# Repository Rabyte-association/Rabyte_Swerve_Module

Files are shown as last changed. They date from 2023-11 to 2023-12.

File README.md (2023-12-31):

# Rabyte_Swerve_Module

---

#8127's custom swerve module design and documentation

## Basic characteristics

- as metric as possibile
- using NEOs for both driving and steering
- using Redux HELIUM Canandcoders
- custom polyurethane cast wheels with printed cores
- 30x60mm profiles for frame
- some 3D printed parts
- gears are modified off-the-shelf metric gears
- 7:64 steering ratio
- 1:7 or 4:21 drive ratio (1 gear swap)
- the design is based on the SDS mk4.

## **[Onshape link](https://cad.onshape.com/documents/77f17ba6a9909df0f0190ebf/w/6d8127f64ed0d1f2707c88a1/e/b61e76f2111f9b8cf438d247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)**

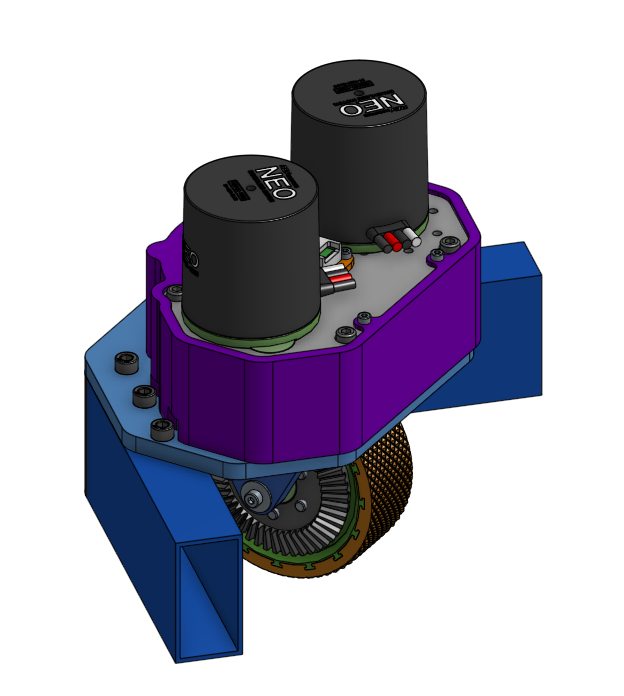
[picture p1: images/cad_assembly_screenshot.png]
cad


## December updates

- 3d printed cover
- new wheel and mould design
- ctre cancoder configuraton
- botom bracket instead of nuts
- config without frame profiles, for easier cad asembly
- added neo spacers, for more clearance

## Drivebase

We designed custom drivebase based on our modules, we are planing to use it in competition.
Onshape link: [drivebase cad link](https://cad.onshape.com/documents/012b6aa6ca8f98a975c3e93b/w/842512061215ac90e2240268/e/b5b0c5cf1ca33fb7e982671a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)
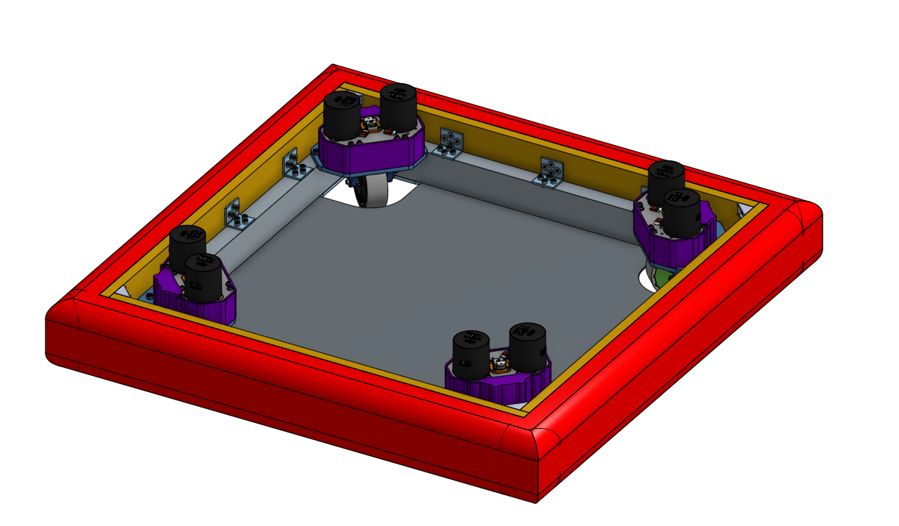
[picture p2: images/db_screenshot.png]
bd


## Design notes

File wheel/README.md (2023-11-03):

# Custom wheels

---

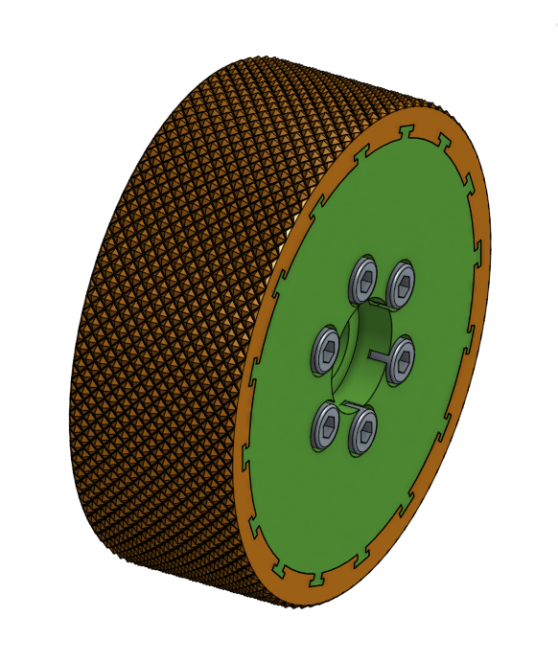
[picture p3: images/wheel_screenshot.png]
wheel


We designed custom 3D printed wheeel with tires casted out of polyurethane. We also did some experiments on how to cast such wheels.

Both  hub and mould are 3D printed. We used 70 shore A polyurethane. That is probably too hard. For the mould release we recomend polivynyl alcohol(pva).

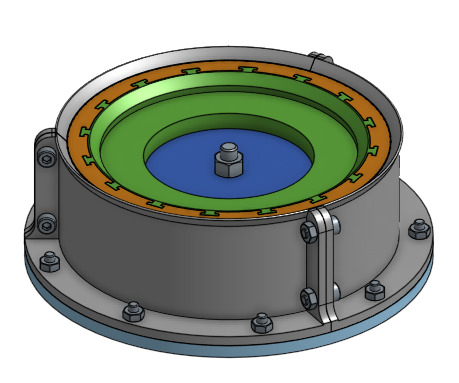
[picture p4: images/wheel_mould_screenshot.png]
mould


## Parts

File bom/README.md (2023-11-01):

# Bill of materials

List of all the necessary parts for one module.

**[google sheets](https://docs.google.com/spreadsheets/d/1GIMMn_G_28G_MlKw39UDYXvYzshxwfw3fDms4F0evjY/edit?usp=sharing)**

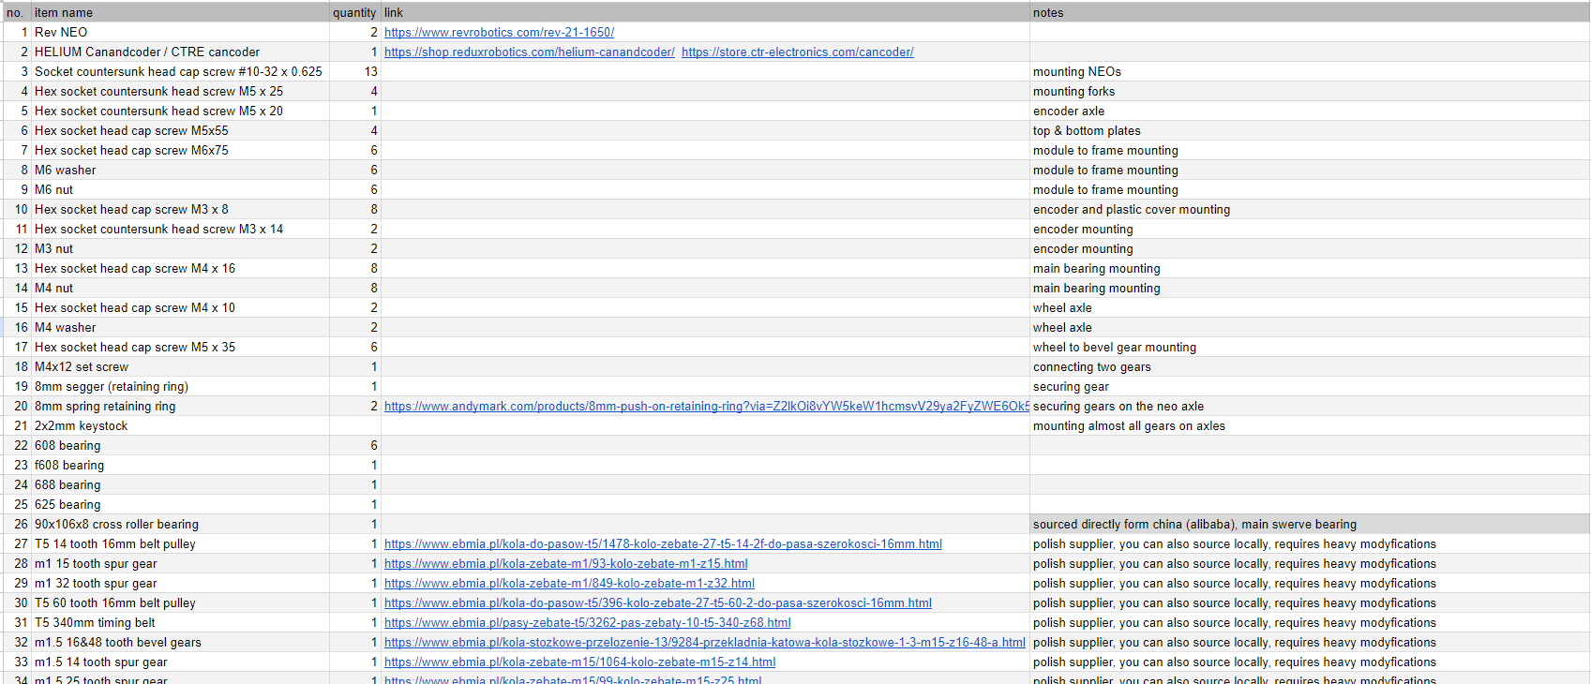
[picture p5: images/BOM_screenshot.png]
sheets


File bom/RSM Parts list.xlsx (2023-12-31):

no. | item name | quantity | link | notes
1 | Rev NEO | 2 | https://www.revrobotics.com/rev-21-1650/
2 | HELIUM Canandcoder / CTRE cancoder | 1 | https://shop.reduxrobotics.com/helium-canandcoder/ https://store.ctr-electronics.com/cancoder/
3 | Socket countersunk head cap screw #10-32 x 0.625 | 13 |  | mounting NEOs
4 | Hex socket countersunk head screw M5 x 25 | 4 |  | mounting forks
5 | Hex socket countersunk head screw M5 x 20 | 1 |  | encoder axle
6 | Hex socket head cap screw M5x55 | 4 |  | top & bottom plates
7 | Hex socket head cap screw M6x75 | 6 |  | module to frame mounting
8 | M6 washer | 6 |  | module to frame mounting
9 | M6 nut | 6 |  | module to frame mounting
10 | Hex socket head cap screw M3 x 8 | 8 |  | encoder and plastic cover mounting
11 | Hex socket countersunk head screw M3 x 14 | 2 |  | encoder mounting
12 | M3 nut | 2 |  | encoder mounting
13 | Hex socket head cap screw M4 x 16 | 8 |  | main bearing mounting
14 | M4 nut | 8 |  | main bearing mounting
15 | Hex socket head cap screw M4 x 10 | 2 |  | wheel axle
16 | M4 washer | 2 |  | wheel axle
17 | Hex socket head cap screw M5 x 35 | 6 |  | wheel to bevel gear mounting
18 | M4x12 set screw | 1 |  | connecting two gears
19 | 8mm segger (retaining ring) | 1 |  | securing gear
20 | 8mm spring retaining ring | 2 | https://www.andymark.com/products/8mm-push-on-retaining-ring | securing gears on the neo axle
21 | 2x2mm keystock |  |  | mounting almost all gears on axles
22 | 608 bearing | 6
23 | f608 bearing | 1
24 | 688 bearing | 1
25 | 625 bearing | 1
26 | 90x106x8 cross roller bearing | 1 |  | sourced directly form china (alibaba), main swerve bearing
27 | T5 14 tooth 16mm belt pulley | 1 | https://www.ebmia.pl/kola-do-pasow-t5/1478-kolo-zebate-27-t5-14-2f-do-pasa-szerokosci-16mm.html | polish supplier, you can also source locally, requires heavy modyfications
28 | m1 15 tooth spur gear | 1 | https://www.ebmia.pl/kola-zebate-m1/93-kolo-zebate-m1-z15.html | polish supplier, you can also source locally, requires heavy modyfications
29 | m1 32 tooth spur gear | 1 | https://www.ebmia.pl/kola-zebate-m1/849-kolo-zebate-m1-z32.html | polish supplier, you can also source locally, requires heavy modyfications
30 | T5 60 tooth 16mm belt pulley | 1 | https://www.ebmia.pl/kola-do-pasow-t5/396-kolo-zebate-27-t5-60-2-do-pasa-szerokosci-16mm.html | polish supplier, you can also source locally, requires heavy modyfications
31 | T5 340mm timing belt | 1 | https://www.ebmia.pl/pasy-zebate-t5/3262-pas-zebaty-10-t5-340-z68.html | polish supplier, you can also source locally, requires heavy modyfications
32 | m1.5 16&48 tooth bevel gears | 1 | https://www.ebmia.pl/kola-stozkowe-przelozenie-13/9284-przekladnia-katowa-kola-stozkowe-1-3-m15-z16-48-a.html | polish supplier, you can also source locally, requires heavy modyfications
33 | m1.5 14 tooth spur gear | 1 | https://www.ebmia.pl/kola-zebate-m15/1064-kolo-zebate-m15-z14.html | polish supplier, you can also source locally, requires heavy modyfications
34 | m1.5 25 tooth spur gear | 1 | https://www.ebmia.pl/kola-zebate-m15/99-kolo-zebate-m15-z25.html | polish supplier, you can also source locally, requires heavy modyfications
35 | m1.5 50 tooth spur gear | 1 | https://www.ebmia.pl/kola-zebate-m15/1785-kolo-zebate-m15-z50.html | polish supplier, you can also source locally, requires heavy modyfications
36 | m1.5 16 tooth spur gear | 1 | https://www.ebmia.pl/kola-zebate-m15/2136-kolo-zebate-m15-z16.html | polish supplier, you can also source locally, requires heavy modyfications, for highr gear ratio
37 | m1.5 12 tooth spur gear | 1 | https://www.ebmia.pl/kola-zebate-m15/211247-kolo-zebate-m15-z12.html | polish supplier, you can also source locally, requires heavy modyfications, for lower gear ratio
38 | top plate | 1 |  | fully custom, aluminium
39 | bottom plate | 1 |  | fully custom, aluminium
40 | power fork | 1 |  | fully custom, steel
41 | passive fork | 1 |  | fully custom, steel
42 | steering axle | 1 |  | fully custom, steel
43 | encoder axle | 1 |  | fully custom, steel
44 | bevel gear axle | 1 |  | fully custom, steel
45 | wheel axle | 1 |  | fully custom, steel
46 | top main bearing mount | 1 |  | fully custom, steel
47 | bottom main bearing mount | 1 |  | fully custom, steel
48 | standoff | 4 |  | fully custom, steel
49 | frame profiles | 2 |  | depends on the design of your robot, we recommend steel 30x60mm
50 | wheel with cast tire | 1 |  | fully custom, 3D printed & cast
51 | encoder mount | 1 |  | fully custom, 3D printed
52 | end cap | 1 |  | fully custom, 3D printed, optional
53 | wheel spacer 1 | 1 |  | fully custom, 3D printed
54 | wheel spacer 2 | 1 |  | fully custom, 3D printed
55
56
57
58
59
60
61
62
63
64
65
66
67
68
69
70
71
72
73
74
75
76
77
78
79
80
81
82
83
84
85
86
87
88
89
90
91
92
93
94
95
96
97
98
99
100
101
102
103
104
105
106
107
108
109
110
111
112
113
114
115
116
117
118
119
120
121
122
123
124
125
126
127
128
129
130
131
132
133
134
135
136
137
138
139
140
141
142
143
144
145
146
147
148
149
150
151
152
153
154
155
156
157
158
159
160
161
162
163
164
165
166
167
168
169
170
171
172
173
174
175
176
177
178
179
180
181
182
183
184
185
186
187
188
189
190
191
192
193
194
195
196
197
198
199
200
201
202
203
204
205
206
207
208
209
210
211
212
213
214
215
216
217
218
219
220
221
222
223
224
225
226
227
228
229
230
231
232
233
234
235
236
237
238
239
240
241
242
243
244
245
246
247
248
249
250
251
252
253
254

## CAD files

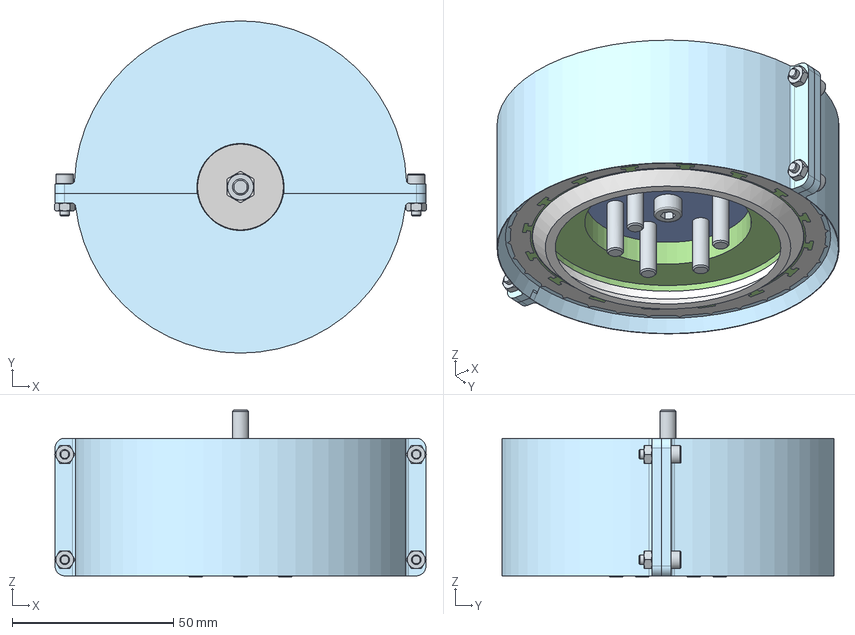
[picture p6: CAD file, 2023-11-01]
wheel/Rabyte_Swerve_Module-wheel_mould_assembly.step
115.4 x 103.0 x 51.7 mm
Hex nut grade A & B M5x0.8
Hex socket head cap screw M3x0.50 x 10 x 4
Hex socket head cap screw M5x0.80 x 35 x 6
Hex nut grade A & B M3x0.5 x 4
tire
hub

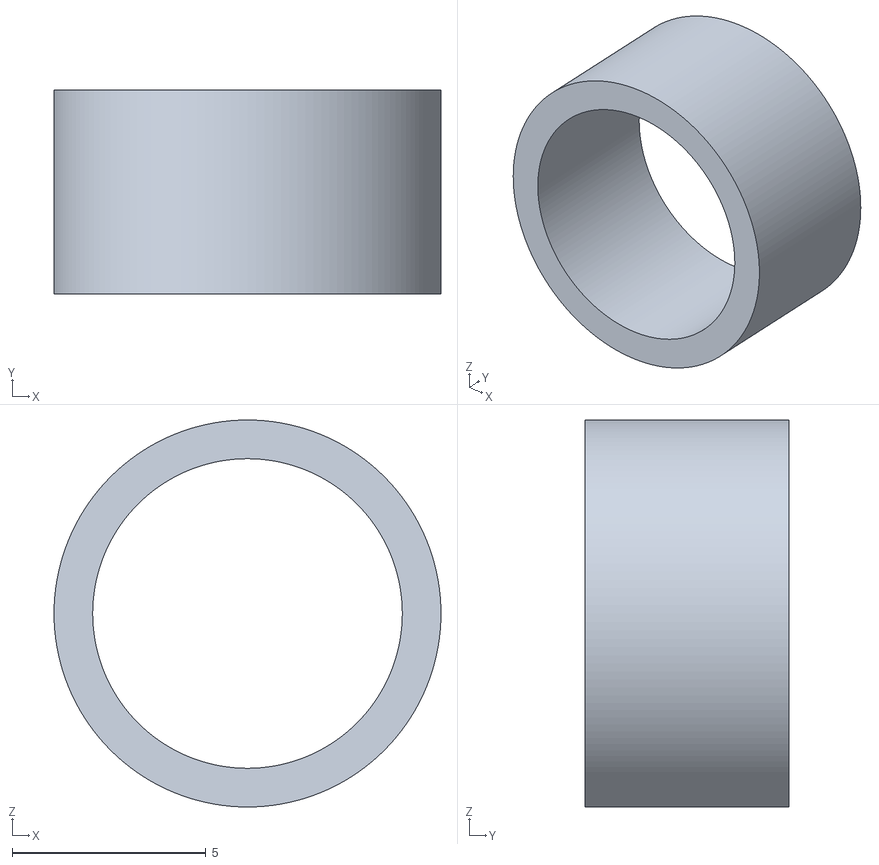
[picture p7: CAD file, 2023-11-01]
3d_print/RSM - main axle - spacer.stl
10.0 x 5.27 x 10.0

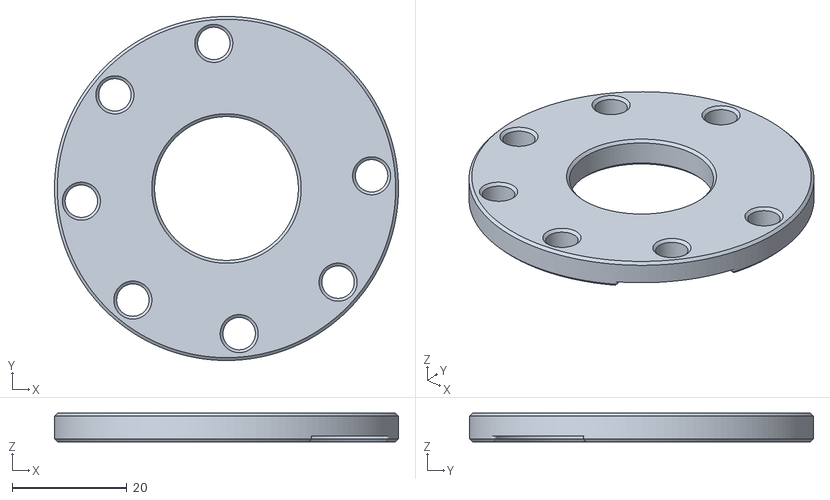
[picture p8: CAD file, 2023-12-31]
3d_print/RSM - neo spacer steer.stl
60.0 x 60.0 x 5.00

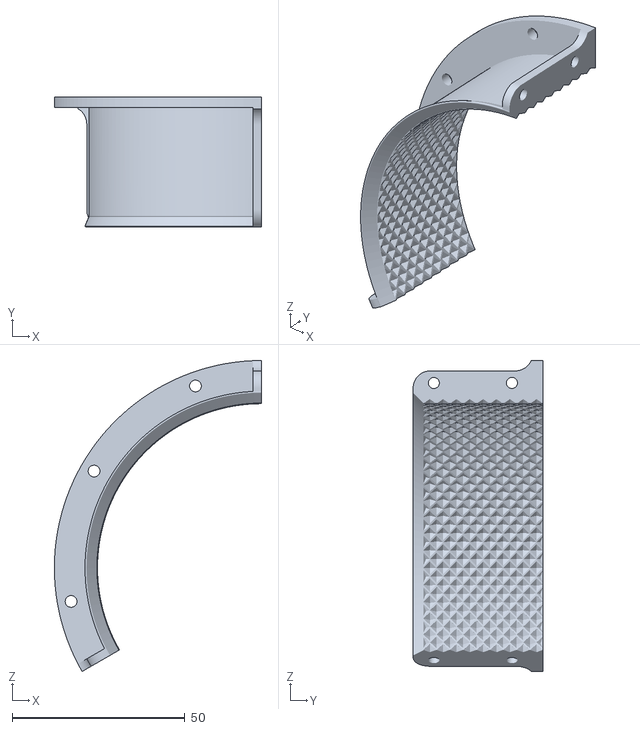
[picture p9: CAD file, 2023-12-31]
wheel/mould - Part 4.stl
60.0 x 37.7 x 90.0

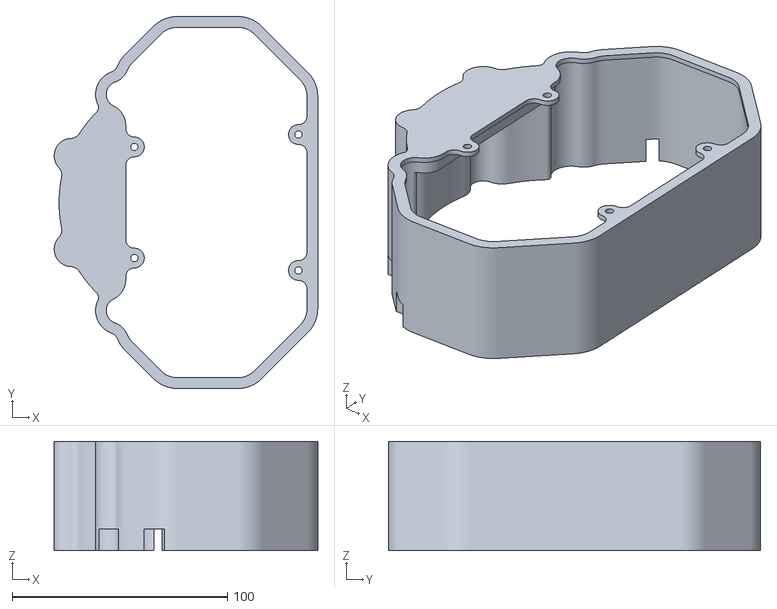
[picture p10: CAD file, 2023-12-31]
3d_print/RSM - cover.stl
122.4 x 172.8 x 50.8

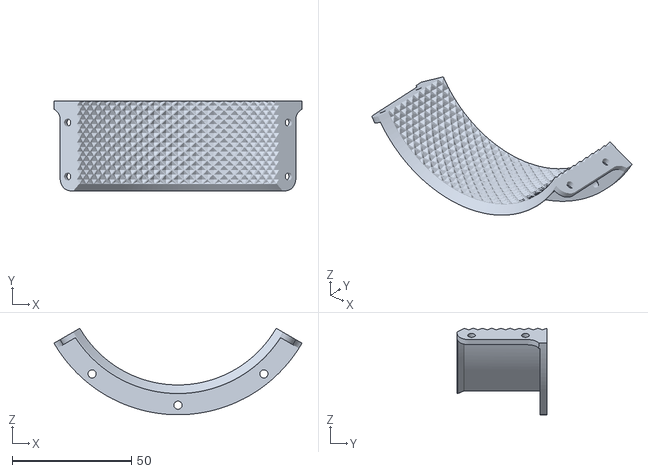
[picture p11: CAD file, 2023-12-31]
wheel/mould - Part 3.stl
103.9 x 37.7 x 36.2

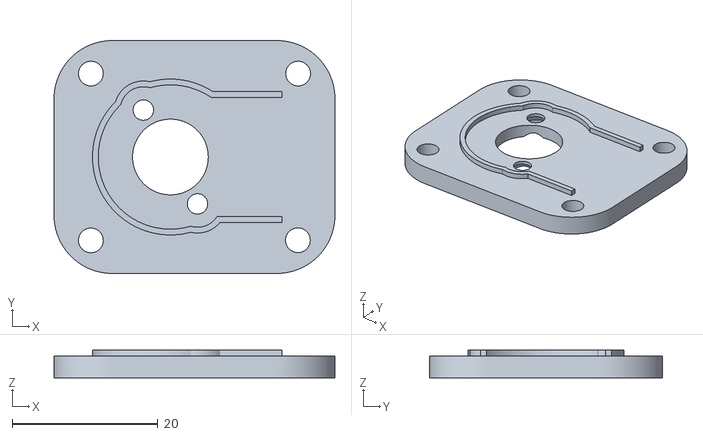
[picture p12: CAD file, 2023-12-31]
3d_print/RSM - canandcoder mount.stl
38.6 x 32.0 x 3.80

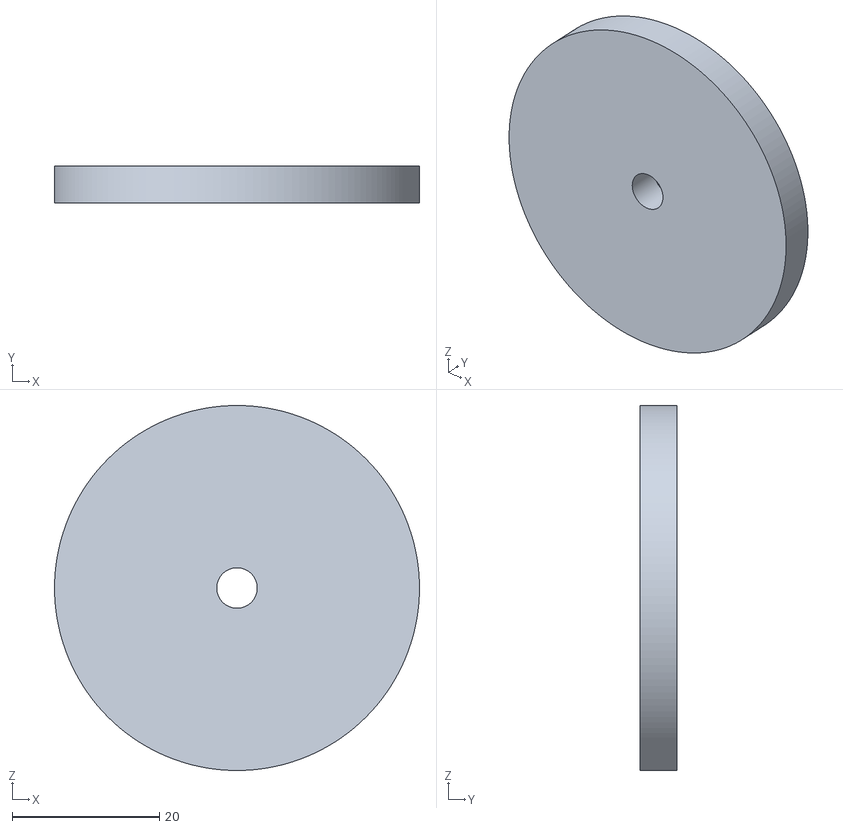
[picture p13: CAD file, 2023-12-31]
wheel/mould - Part 5.stl
49.6 x 5.00 x 49.6

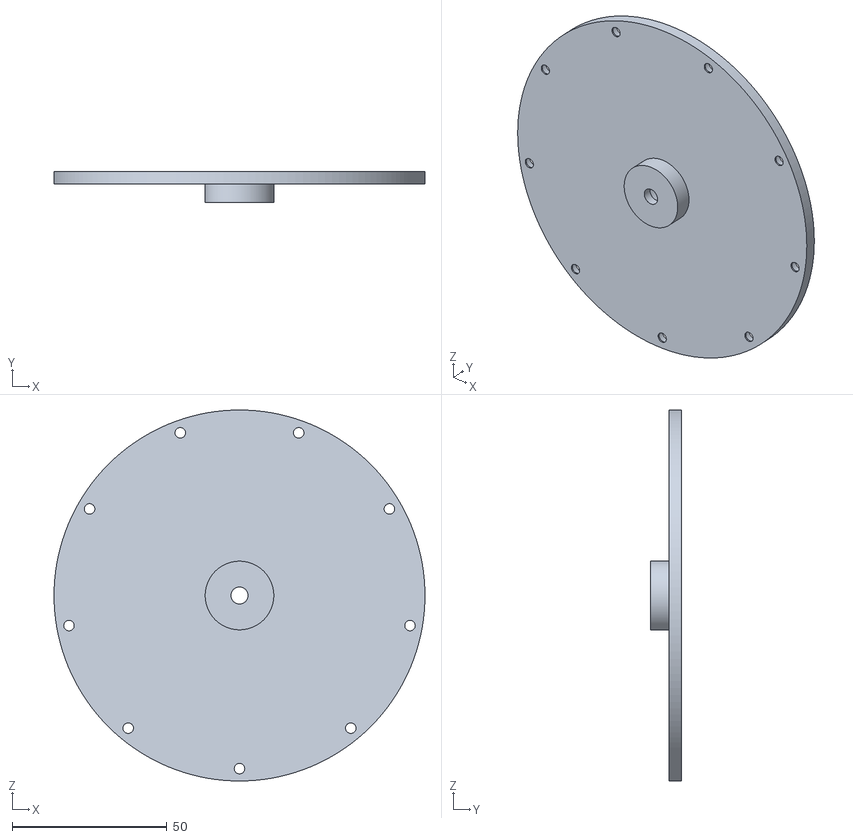
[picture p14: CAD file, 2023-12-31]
wheel/mould - Part 1.stl
120.0 x 10.0 x 120.0

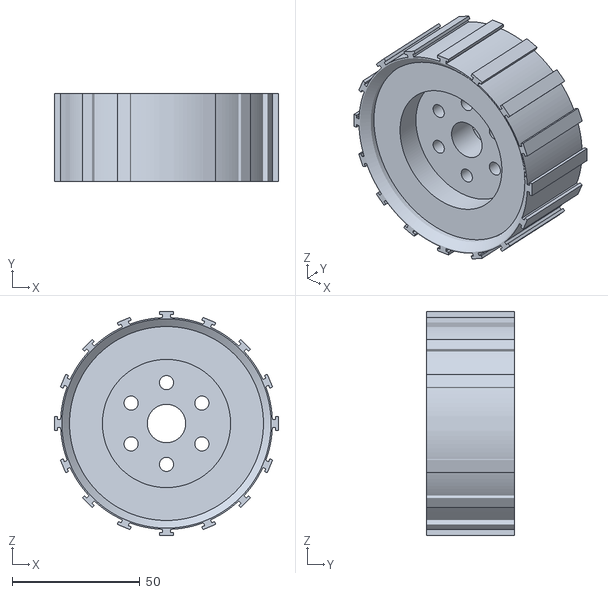
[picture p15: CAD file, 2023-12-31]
wheel/RSM-wheel_hub.stl
87.7 x 34.7 x 87.7

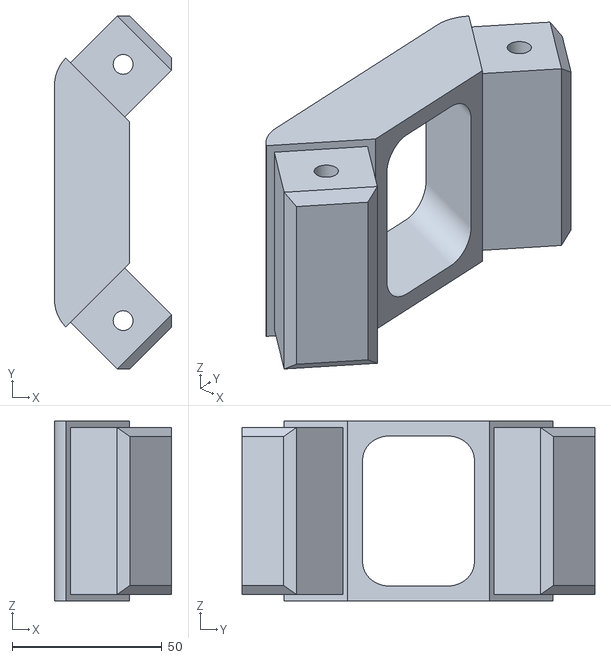
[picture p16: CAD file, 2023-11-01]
3d_print/RSM - end cap.stl
39.0 x 117.7 x 60.0

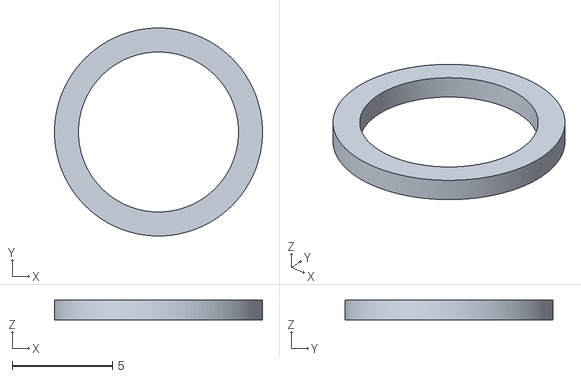
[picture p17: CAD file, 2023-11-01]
3d_print/RSM - 608 spacer - 1mm spacer.stl
10.4 x 10.4 x 1

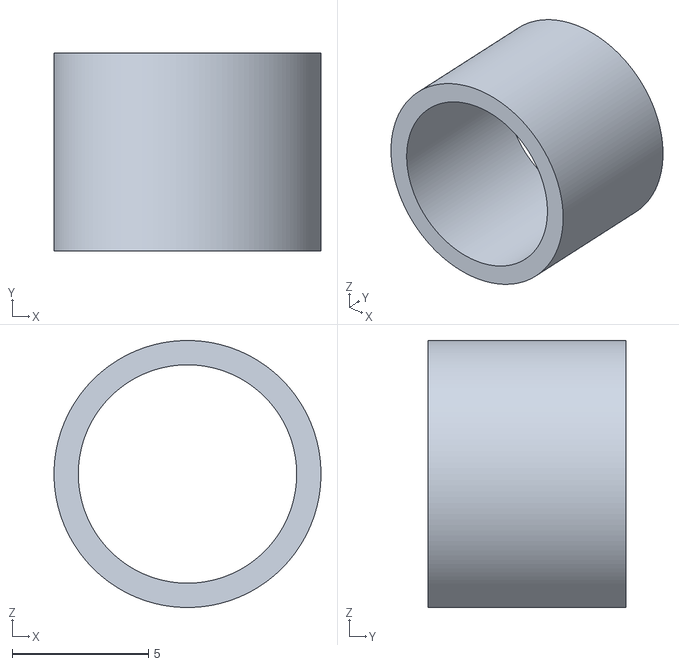
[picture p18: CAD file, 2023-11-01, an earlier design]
3d_print/RSM - main axle - spacer (1).stl
9.78 x 7.27 x 9.78

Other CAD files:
3d_print/RSM - cancoder mount.stl
wheel/mould - Part 2.stl
3d_print/RSM - neo spacer drive.stl

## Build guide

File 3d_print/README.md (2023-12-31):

# 3D printed parts

---
Some of the parts in the module are 3D printed.
Printing settings:

- PLA is **not** good enough
- around 5 walls, for strength
- infill around 50%, also for strength
- supports: not required for most parts

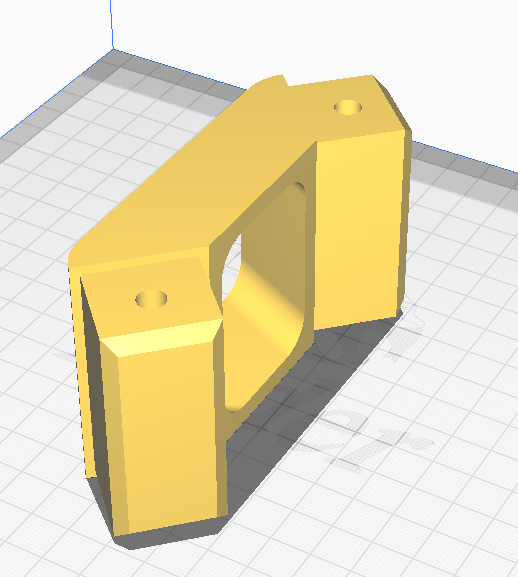
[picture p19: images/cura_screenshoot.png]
cura


As a side note, we printed the whole set of gears, forks and plates and it mostly works. Of course we don't recomend using it in the competiton, however it was a great resource for the programming team while we were waiting for the machined parts.

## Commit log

2023-11-01 cad upload
    [RSM-1mm_608_spacer.stl, RSM-beam_end_cap.stl, RSM-canandcoder_mount.stl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]
2023-11-01 some documentation
    [RSM Parts list.xlsx]
2023-11-01 wheel documentation
2023-12-31 deceber updates
    [RSM - 608 spacer - 1mm spacer.stl, RSM - canandcoder mount.stl, RSM - cancoder mount.stl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]
